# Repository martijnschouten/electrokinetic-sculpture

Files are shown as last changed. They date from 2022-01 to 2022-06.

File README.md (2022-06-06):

# Electrokinetic sculpture
This sculpture has been built as a demonstration of electrical friction compensation. The sculpture aims to create the same long-lasting mesmerizing effect as the work of [David C. Roy](https://www.woodthatworks.com/), but with cheap mechanical components, 3D printed parts and smart electronics. 

The sculpture currently has two modes. There is interactive mode in which it is possible to interact with the front wheel. In this cases the front wheel reacts as if it was connected to a passive system with little friction and a large moment of inertia. To see a video of the interactive mode click [here](https://youtu.be/oQwkW7BH-mE). The second mode is a zen mode in this mode the sculpture just rotates slowly, a video of this mode can be found [here](https://youtu.be/FcRmKU-JQ9s "Video on Youtube")

PXL_20220102_092019050-2 MP (https://youtu.be/oQwkW7BH-mE "Video on Youtube")

For a more detailed description of the project see the [hackaday page](https://hackaday.io/project/183344-electrokinetic-sculpture).

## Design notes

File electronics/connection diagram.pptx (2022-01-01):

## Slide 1

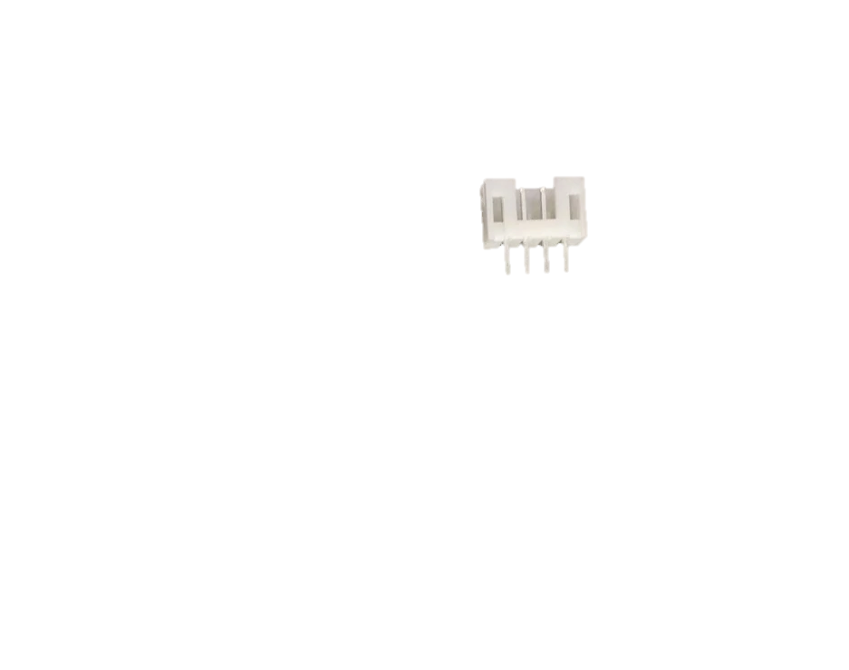
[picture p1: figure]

Charging port

Front wheel

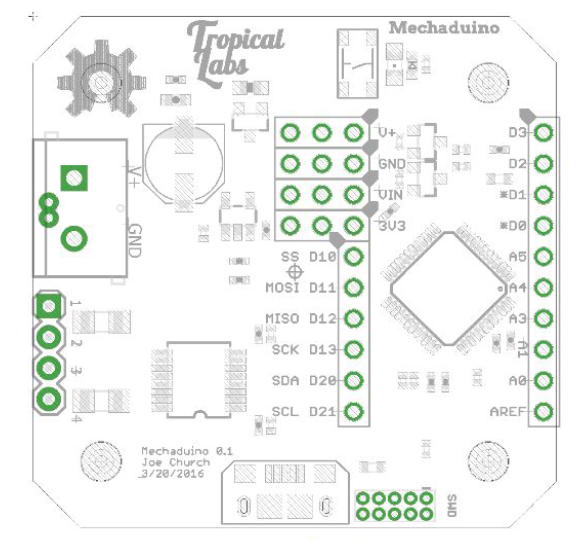
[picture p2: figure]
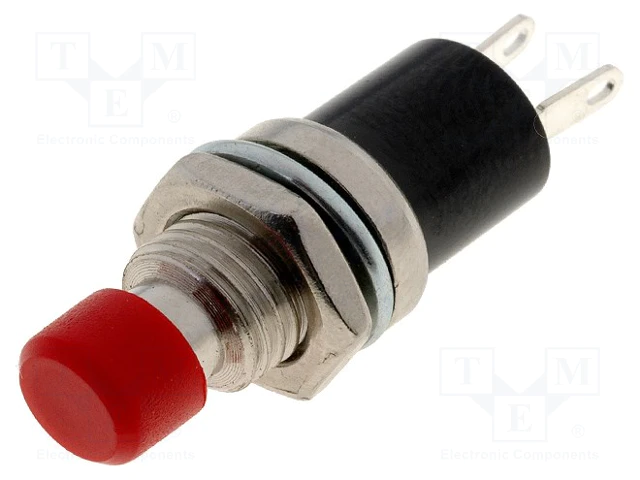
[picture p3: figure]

Program button

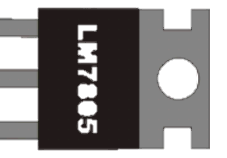
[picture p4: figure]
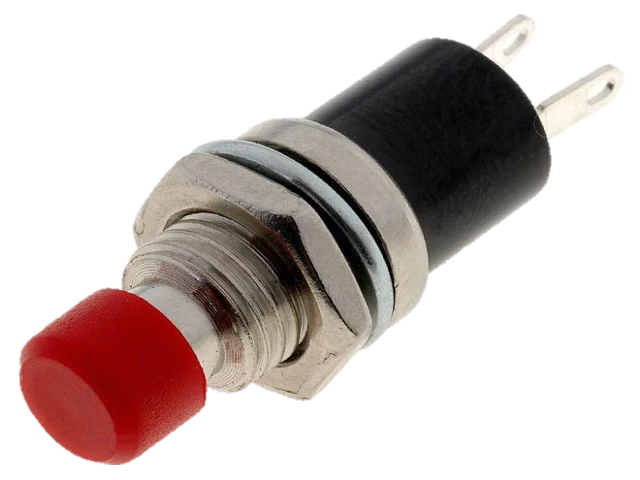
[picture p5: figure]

Mode Select

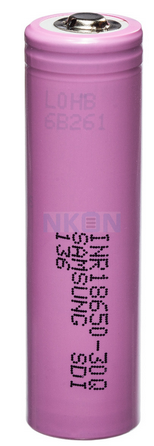
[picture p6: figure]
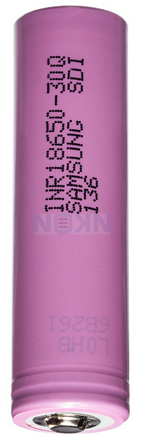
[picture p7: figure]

BMS

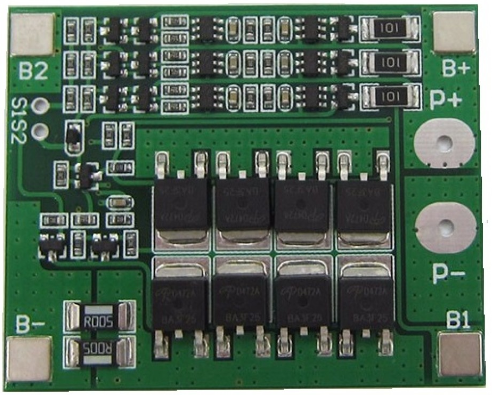
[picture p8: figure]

On/Off
Switch

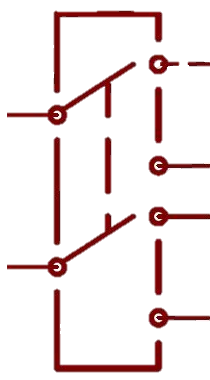
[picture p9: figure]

Back wheel

Program button

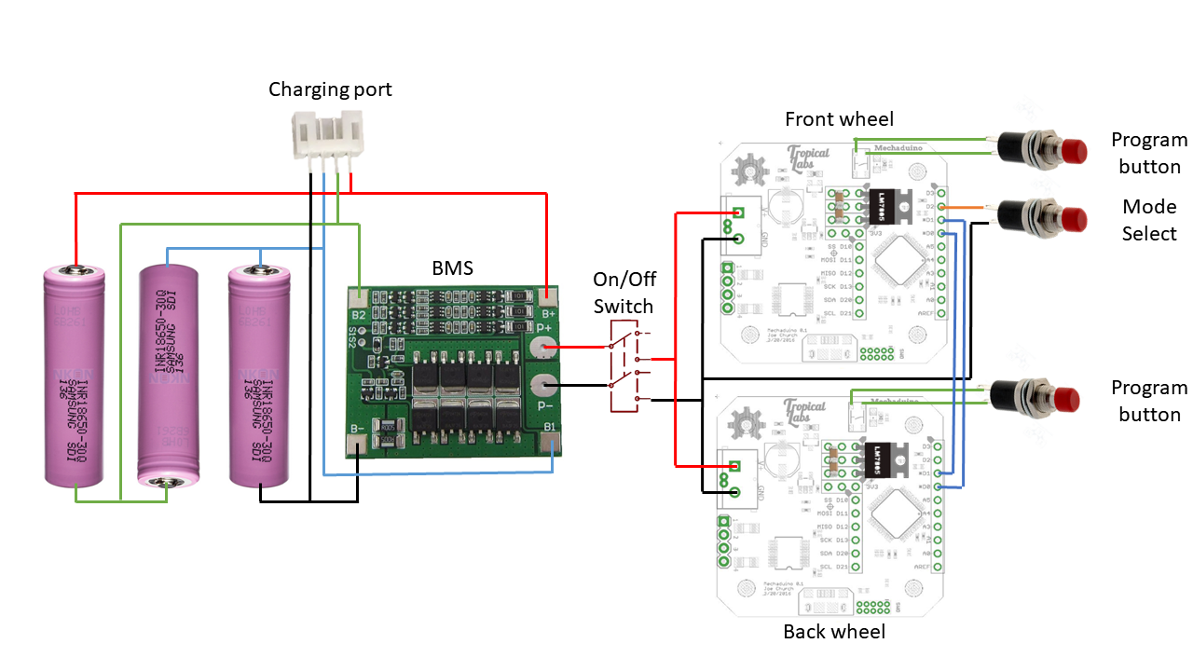
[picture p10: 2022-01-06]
electronics/connection diagram.png

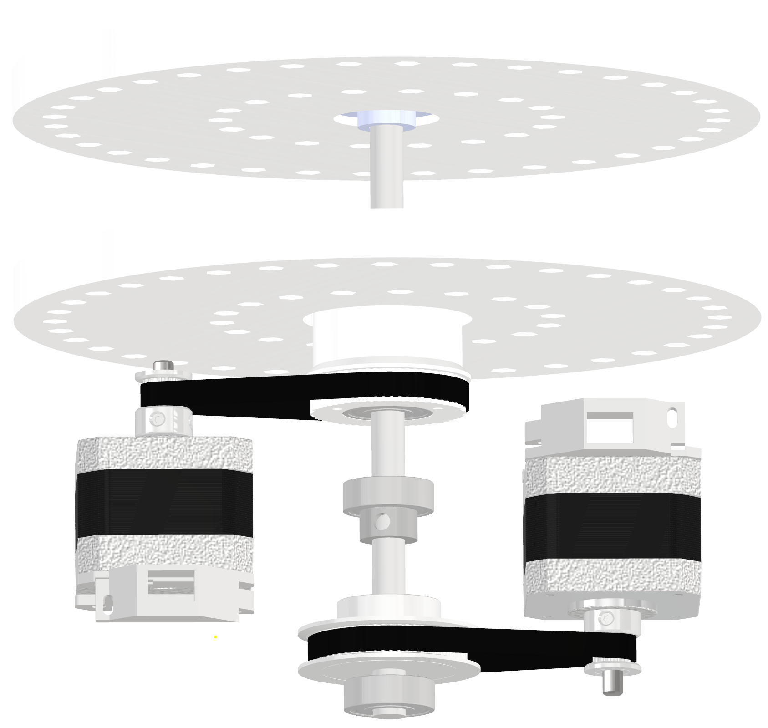
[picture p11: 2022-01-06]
cad files/mechanics view.png

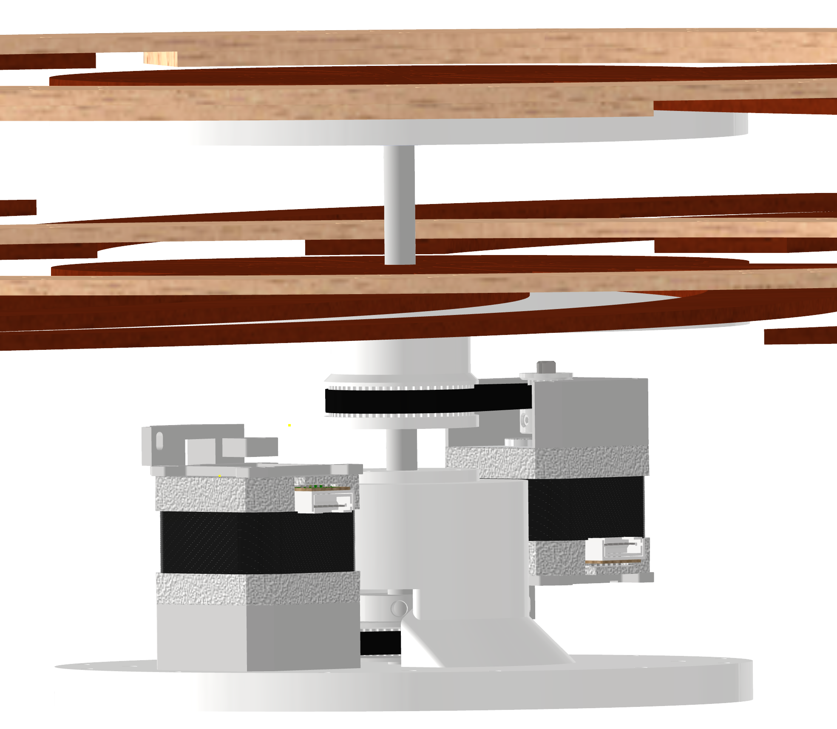
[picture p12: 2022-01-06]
cad files/inside view.png

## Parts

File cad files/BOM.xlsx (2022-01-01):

123-3d
1 | BMS | 4.5 | 2.95 | 7.45 | https://www.tinytronics.nl/shop/en/batteries/other/li-ionli-po-protection-circuit-(bms)-3s
2 | Stepper | 12.5 | 6.95 | 31.95 | https://www.123-3d.nl/123-3D-NEMA17-stappenmotor-1-8-graden-per-stap-40-mm-lang-4-08-kg-cm-SL42S240A105-0524-i3421-t14804.html
1 | pulley 60 teeth | 10 | 0 | 10 | https://www.123-3d.nl/123-3D-GT2-Pulley-hoge-resolutie-6-mm-riem-60-tanden-8-mm-as-i2572-t14819.html
2 | pulley 16 teeth | 6 | 0 | 12 | https://www.123-3d.nl/123-3D-GT2-Pulley-hoge-resolutie-6-mm-riem-16-tanden-5-mm-as-14-mm-hoog-6GT2DR16T5MMD-i2114-t14815.html
1 | mounting hub | 8 | 2.95 | 10.95 | https://opencircuit.shop/Product/Pololu-Universal-Aluminum-Mounting-Hub-8mm
3 |  | 2.75 | 0 | 8.25 | https://www.123-3d.nl/123-3D-Metaalschroef-inbus-M3x20-cilinderkop-verzinkt-50-stuks-i1175-t3122.html
2 |  | 2.25 | 0 | 4.5 | https://www.123-3d.nl/123-3D-Metaalschroef-inbus-M3x12-cilinderkop-verzinkt-50-stuks-i1173-t3122.html
2 |  | 2.5 | 0 | 5 | https://www.123-3d.nl/123-3D-Zeskantmoer-verzinkt-M3-100-stuks-i130-t3042.html
4 |  | 0.75 | 0 | 3 | https://www.123-3d.nl/123-3D-Kogellager-608ZZ-DME00003-i20-t13131.html
1 |  | 27.5 | 0 | 27.5 | https://www.123-3d.nl/123-3D-Filament-wit-1-75-mm-PETG-1-kg-Jupiter-serie-DFE02013c-i1907-t7395.html
1 |  | 12.5 | 0 | 12.5 | https://www.123-3d.nl/123-3D-Lineaire-as-staaf-gehard-en-geslepen-met-chroomlaag-8x250-mm-i1775-t13814.html
2 |  | 5.95 | 2.95 | 14.85 | https://www.kiwi-electronics.nl/panel-mount-usb-b-naar-micro-b-kabel?lang=en
 |  |  |  | 100 | laser cutting
 |  |  |  | 247.95
additional
1 |  | 13.99 | 6.95 | 20.94 | https://www.conrad.nl/p/voltcraft-eco-lipo-1000-modelbouw-oplader-230-v-1-a-li-poly-1460626
china
1 | BMS | 4.5 | 2.95 | 7.45 | https://www.tinytronics.nl/shop/en/batteries/other/li-ionli-po-protection-circuit-(bms)-3s
2 | Stepper | 12.5 | 6.95 | 31.95 | https://www.123-3d.nl/123-3D-NEMA17-stappenmotor-1-8-graden-per-stap-40-mm-lang-4-08-kg-cm-SL42S240A105-0524-i3421-t14804.html
1 | pulley 60 teeth | 1 | 2.22 | 3.22 | https://www.123-3d.nl/123-3D-GT2-Pulley-hoge-resolutie-6-mm-riem-60-tanden-8-mm-as-i2572-t14819.html
2 | pulley 16 teeth | 0.7 | 2.22 | 3.62 | https://www.aliexpress.com/item/32950478691.html
1 | mounting hub | 8 | 2.95 | 10.95 | https://opencircuit.shop/Product/Pololu-Universal-Aluminum-Mounting-Hub-8mm
3 |  | 2.75 | 0 | 8.25 | https://www.123-3d.nl/123-3D-Metaalschroef-inbus-M3x20-cilinderkop-verzinkt-50-stuks-i1175-t3122.html
2 |  | 2.25 |  | 4.5 | https://www.123-3d.nl/123-3D-Metaalschroef-inbus-M3x12-cilinderkop-verzinkt-50-stuks-i1173-t3122.html
2 |  | 2.5 |  | 5 | https://www.123-3d.nl/123-3D-Zeskantmoer-verzinkt-M3-100-stuks-i130-t3042.html
4 |  | 0.75 |  | 3 | https://www.123-3d.nl/123-3D-Kogellager-608ZZ-DME00003-i20-t13131.html
1 |  | 27.5 |  | 27.5 | https://www.123-3d.nl/123-3D-Filament-wit-1-75-mm-PETG-1-kg-Jupiter-serie-DFE02013c-i1907-t7395.html
1 |  | 4 |  | 4 | https://www.123-3d.nl/123-3D-Lineaire-as-staaf-gehard-en-geslepen-met-chroomlaag-8x250-mm-i1775-t13814.html
2 |  | 5.95 | 2.95 | 14.85 | https://www.kiwi-electronics.nl/panel-mount-usb-b-naar-micro-b-kabel?lang=en
 |  |  |  | 100 | laser cutting
 |  |  |  | 224.29

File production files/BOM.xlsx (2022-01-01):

Needed | Name | Units | Cost | Shipping | Total | Link
1 | Li-ion/Li-Po Protection circuit (BMS) - 3S - with Balancing | 1 | 4.5 | 2.95 | 7.45 | https://www.tinytronics.nl/shop/en/batteries/other/li-ionli-po-protection-circuit-(bms)-3s
2 | NEMA17, 40mm long 1,8 degree per step | 2 | 12.5 | 6.95 | 31.95 | https://www.123-3d.nl/123-3D-NEMA17-stappenmotor-1-8-graden-per-stap-40-mm-lang-4-08-kg-cm-SL42S240A105-0524-i3421-t14804.html
1 | GT2 Pulley, 6 mm belt, 60 teeth, 8 mm axis | 1 | 10 | 0 | 10 | https://www.123-3d.nl/123-3D-GT2-Pulley-hoge-resolutie-6-mm-riem-60-tanden-8-mm-as-i2572-t14819.html
2 | GT2 Pulley, 6 mm belt, 16 teeth, 5 mm axis, 14 mm long | 2 | 6 | 0 | 12 | https://www.123-3d.nl/123-3D-GT2-Pulley-hoge-resolutie-6-mm-riem-16-tanden-5-mm-as-14-mm-hoog-6GT2DR16T5MMD-i2114-t14815.html
1 | Pololu Universal Aluminum Mounting Hub for 8mm Shaft, M3 Holes | 1 | 8 | 2.95 | 10.95 | https://opencircuit.shop/Product/Pololu-Universal-Aluminum-Mounting-Hub-8mm
186 | m3 x 16 50pcs | 4 | 2.7 | 0 | 10.8 | https://www.123-3d.nl/123-3D-Metaalschroef-inbus-M3x16-cilinderkop-verzinkt-50-stuks-i1174-t3122.html
168 | m3 locknut 100pcs | 2 | 3.2 | 0 | 6.4 | https://www.123-3d.nl/123-3D-Borgmoer-verzinkt-M3-100-stuks-i132-t3043.html
8 | m3 x 35 50 pcs | 1 | 3.5 | 0 | 3.5 | https://www.123-3d.nl/123-3D-Metaalschroef-inbus-M3x35-cilinderkop-verzinkt-50-stuks-i1178-t3122.html
4 | 608ZZ ball bearing | 4 | 0.75 | 0 | 3 | https://www.123-3d.nl/123-3D-Kogellager-608ZZ-DME00003-i20-t13131.html
2 | 1kg PLA white | 2 | 27.5 | 0 | 55 | https://www.123-3d.nl/123-3D-Filament-wit-1-75-mm-PETG-1-kg-Jupiter-serie-DFE02013c-i1907-t7395.html
1 | 8x250 mm axis | 1 | 12.5 | 0 | 12.5 | https://www.123-3d.nl/123-3D-Lineaire-as-staaf-gehard-en-geslepen-met-chroomlaag-8x250-mm-i1775-t13814.html
2 | Panel Mount USB B to Micro-B cable | 2 | 5.95 | 2.95 | 14.85 | https://www.kiwi-electronics.nl/en/panel-mount-usb-b-to-micro-b-cable-901
1 | laser cutting, 6mm Birch Plywood | 1 | 181 | 0 | 181 | https://snijlab.nl/
2 | GT2 timing belt, 6 mm, closed, 188 mm | 2 | 3.5 | 0 | 7 | https://www.123-3d.nl/123-3D-GT2-timing-belt-6-mm-gesloten-188-mm-i2748-t3046.html
1 | VOLTCRAFT Eco LiPo 1000 charger | 1 | 13.99 | 6.95 | 20.94 | https://www.conrad.nl/p/voltcraft-eco-lipo-1000-modelbouw-oplader-230-v-1-a-li-poly-1460626
2 | Mechaduino | 2 | 49 | 0 | 98 | https://tropical-labs.com/shop/mechaduino-0-2-pcb/
3 | PS-01 red push button | 1 | 1.19 | 0 | 1.19 | https://www.tme.eu/en/details/ps-01/standard-switches/
1 | TSX103 dpdt switch 3A | 1 | 1.17 | 0 | 1.17 | https://www.tme.eu/en/details/tsx103/toggle-switches/ninigi/
2 | JST PH 4P | 1 | 1.27 | 1.99 | 3.26 | https://www.aliexpress.com/item/4000091077742.html
3 | Samsung INR18650-30Q 3000mAh - 15A button top | 3 | 7.95 | 0 | 23.85 | https://www.nkon.nl/samsung-inr-18650-30q-3000mah-button-top.html
3 | 10pcs 18650 Battery holder | 1 | 5.51 | 0 | 5.51 | https://www.aliexpress.com/item/32858162000.html
400ml | Rambo warm oak silk | 1 | 28.99 | 0 | 28.99 | https://www.karwei.nl/assortiment/rambo-pantserlak-interieur-transparant-zijdeglans-warm-eiken-750-ml/p/B607934
150ml | cetabever transparent silk | 1 | 24.49 | 0 | 24.49 | https://www.karwei.nl/assortiment/cetabever-binnenbeits-transparant-zijdeglans-beuken-750-ml/p/B183112
2 | L7805abv voltage regulator | 2 | 0.33 | 0 | 0.66 | https://www.tme.eu/en/details/l7805abv/unregulated-voltage-regulators/stmicroelectronics/
4 | 0805 1uF capacitor | 4 | 0.01 | 0 | 0.04
 |  |  |  |  | 574.5

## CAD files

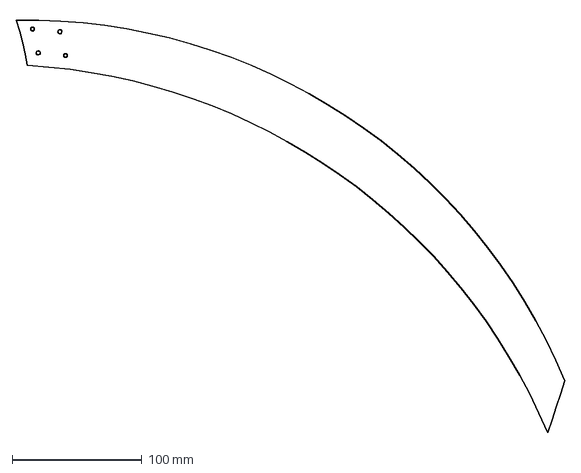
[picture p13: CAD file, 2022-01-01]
production files/laser cutting/6x spoke4 6mm.dxf
423.3 x 321.5 mm

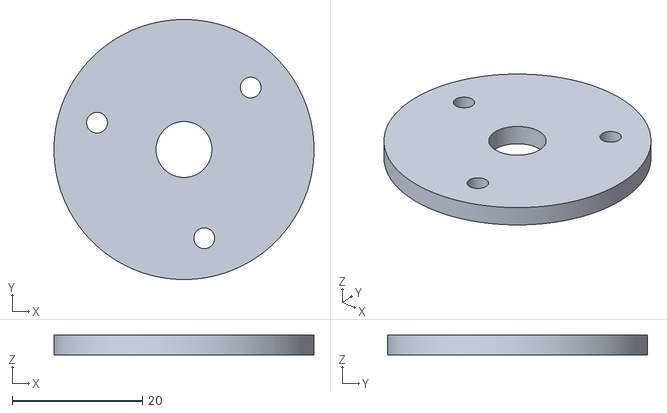
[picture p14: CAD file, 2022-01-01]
production files/stls/sculpture_bearing_holder.stl
40.0 x 40.0 x 3.00

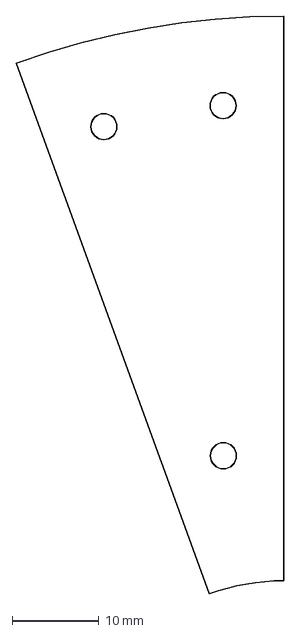
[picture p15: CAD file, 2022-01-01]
production files/laser cutting/12x cover 6mm.dxf
30.8 x 66.5 mm

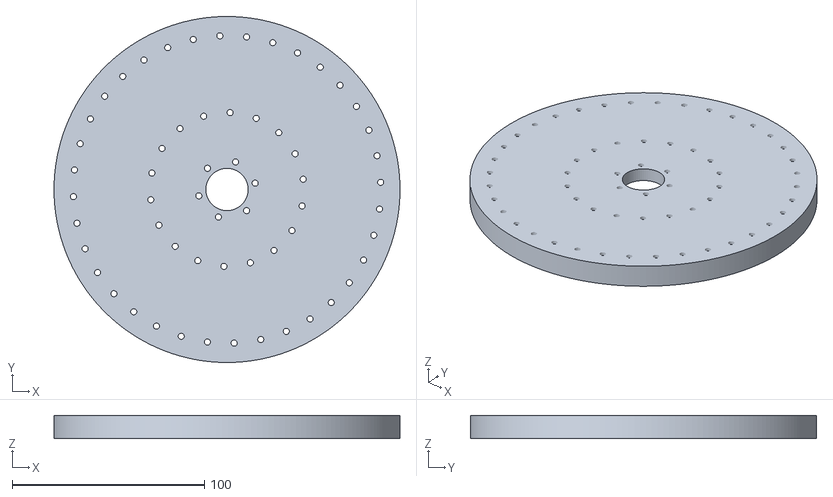
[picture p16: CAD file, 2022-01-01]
production files/stls/sculpture_pulley1.stl
180.0 x 180.0 x 12.0

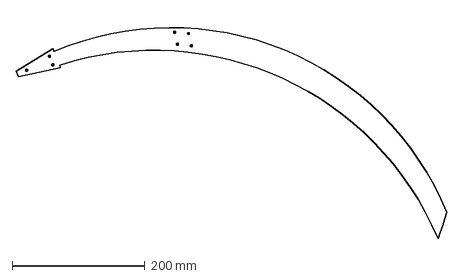
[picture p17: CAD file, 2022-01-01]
production files/laser cutting/6x spoke 6mm.dxf
649.7 x 335.7 mm

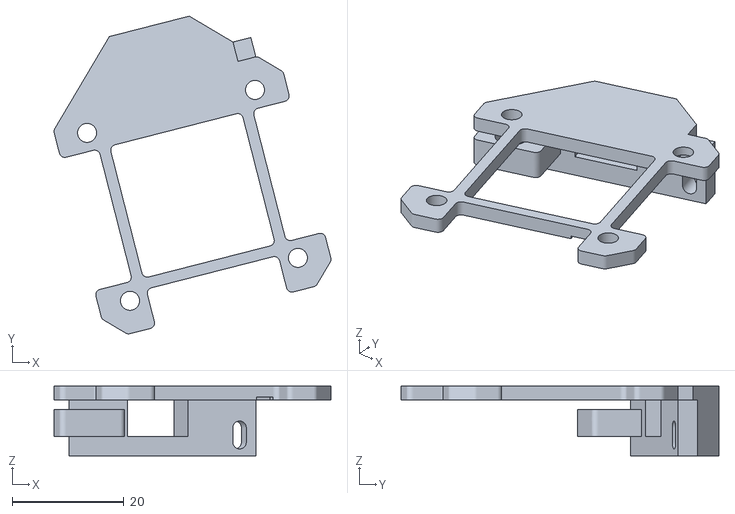
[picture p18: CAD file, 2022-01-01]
production files/stls/sculpture_mechaduino_mount3.stl
49.5 x 56.8 x 12.5

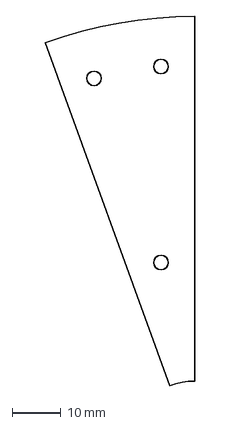
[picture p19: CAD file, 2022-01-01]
production files/laser cutting/12x cover2 6mm.dxf
30.8 x 75.9 mm

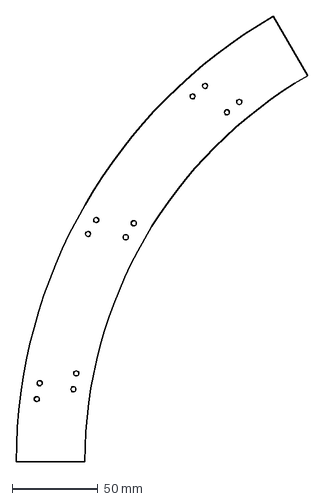
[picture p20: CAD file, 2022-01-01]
production files/laser cutting/4x wheel6 6mm.dxf
170.0 x 259.8 mm

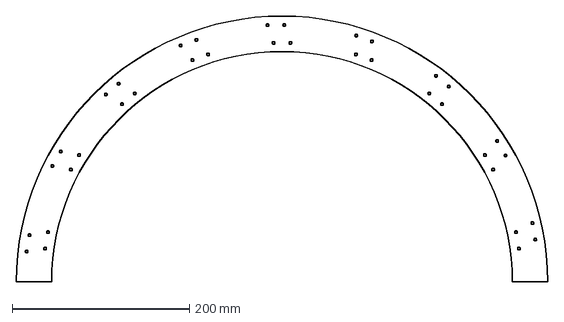
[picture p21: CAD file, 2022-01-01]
production files/laser cutting/4x wheel 6mm.dxf
600.0 x 300.0 mm

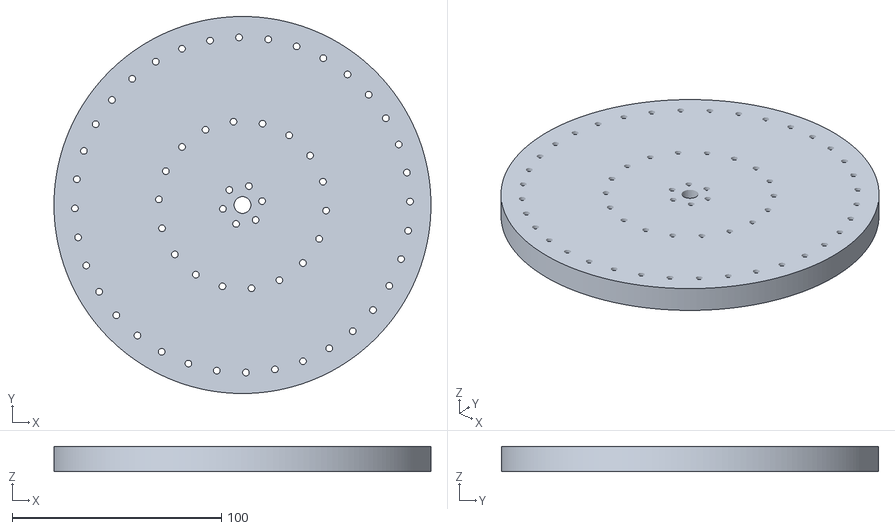
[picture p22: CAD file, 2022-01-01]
production files/stls/sculpture_front_plate.stl
180.0 x 180.0 x 12.0

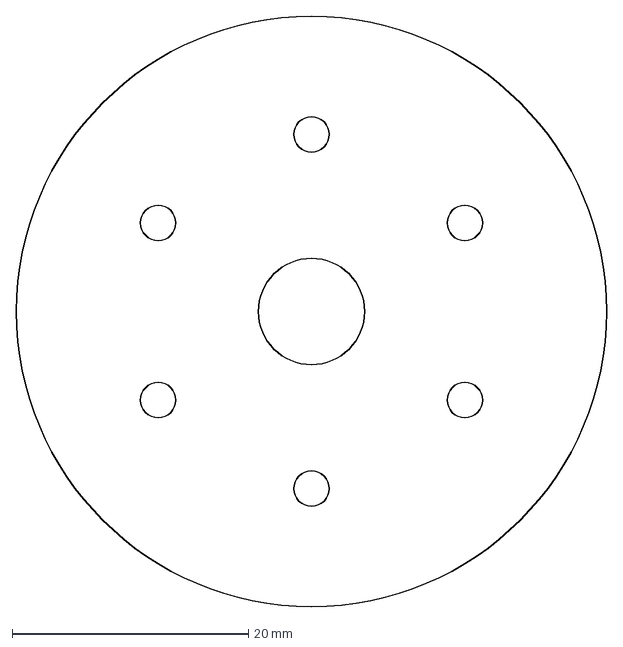
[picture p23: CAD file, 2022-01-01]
production files/laser cutting/1x circle2 6mm.dxf
50.0 x 50.0 mm

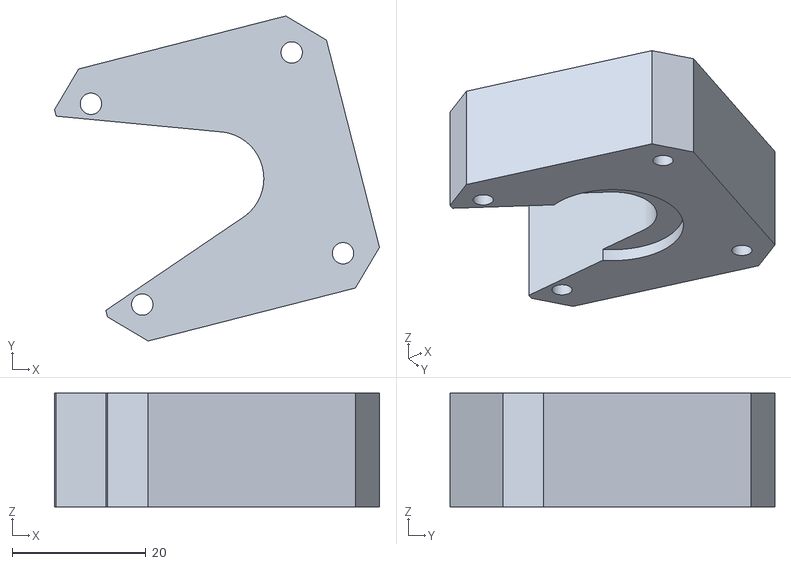
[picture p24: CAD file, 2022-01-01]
production files/stls/sculpture_motor_spacer_1.stl
48.6 x 48.6 x 17.0

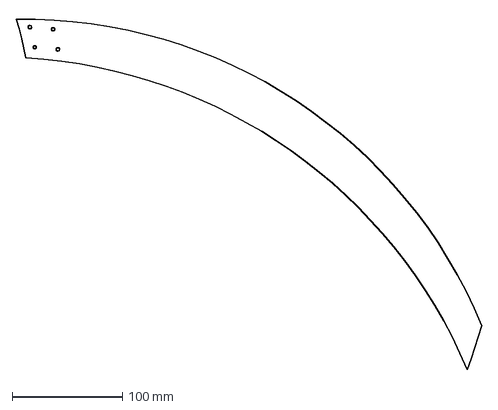
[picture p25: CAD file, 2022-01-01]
production files/laser cutting/6x spoke2 6mm.dxf
423.3 x 321.5 mm

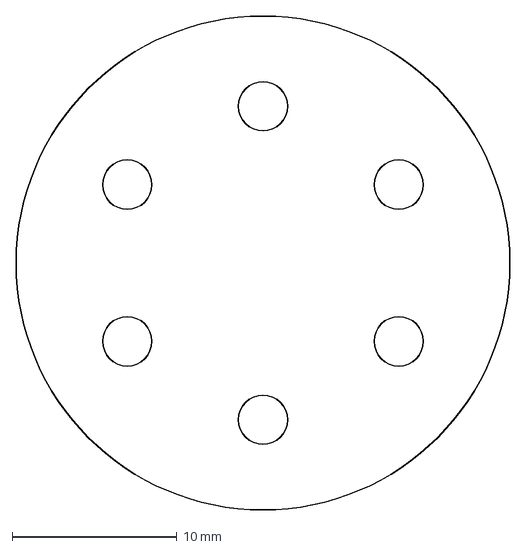
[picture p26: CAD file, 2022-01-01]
production files/laser cutting/1x circle 6mm.dxf
30.0 x 30.0 mm

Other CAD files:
production files/stls/sculpture_bearing_holder2.stl
production files/stls/sculpture_mechaduino_mount3_1.stl
production files/stls/sculpture_motor_spacer.stl
production files/stls/sculpture_wall_mount.stl
cad files/Assembly1.iam
cad files/GT2 60 teeth pulley.ipt
cad files/GT2_16T.ipt
cad files/Lock Collar 8mm.ipt
cad files/Nema 17 - Busheng 17HD34008-22B/ANSI B27.7 - 53.9(1).ipt
cad files/Nema 17 - Busheng 17HD34008-22B/BS 3469 - 02 - 5 x 16 x 5.ipt
cad files/Nema 17 - Busheng 17HD34008-22B/EN ISO 7045 - M3 x 25H.ipt
cad files/Nema 17 - Busheng 17HD34008-22B/Nema 17 Base Cap.ipt
cad files/Nema 17 - Busheng 17HD34008-22B/Nema 17 Central Spacer.ipt
cad files/Nema 17 - Busheng 17HD34008-22B/Nema 17 Coil.ipt
cad files/Nema 17 - Busheng 17HD34008-22B/Nema 17 PCB.ipt
cad files/Nema 17 - Busheng 17HD34008-22B/Nema 17 Plastic Spacer 1.ipt
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

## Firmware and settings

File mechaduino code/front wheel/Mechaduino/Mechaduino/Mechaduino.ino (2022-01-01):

 /*
  Author: Martijn Schouten
  Contact: https://github.com/martijnschouten/

  To use this program you first need to calibrate your mechaduino. To do so:
  - Upload the project in the for calibration folder
  - Go to the serial monitor and connect to your mechaduino
  - Start the calibration routine by sending c to your mechaduino. Make sure it is free to rotate.
  - Copy the outputted encoder lookup table to parameters.cpp

  To make this run stably on your hardware you may have to tune T_static, d_term (current file) and vKp, vKi, vKd (parameters.cpp)
*/

#include "Utils.h"
#include "Parameters.h"
#include "State.h"
#include "analogFastWrite.h"
#include <arduino-timer.h>


//////////////////////////////////////
/////////////////SETUP////////////////
//////////////////////////////////////

//Velocity calculation
float yw_old = 0;         //Last measured position
float v_loc = 0;          //Low pass filtered velocity estimate
float v_a = 0.7265;       //a coefficient of the low pass filter on the velocity
float v_b = 0.1367;       //b coefficient of the low pass filter on the velocity

//Acceleration calculation
float v_old = 0;          //Last calculated velocity
float a_loc = 0;          //Low pass filtered acceleration estimate
float a_a = 0.9691;       //a coefficient of the low pass filter on the acceleration
float a_b = 0.0155;       //b coefficient of the low pass filter on the acceleration

//Friction compensation
float T_static = 20;      //Estimate of the current needed to overcome the static friction in mA and divided by 8.6 
float v_idle = 0.04;      //Velocity above which the static friction compensation will become active
float p_term = 0.1;       //Determines the stiffness of the spring when rotated in the clockwise direction
float d_term = -10;       //Estimate of the dynamic friction
float m_term = 5000;      //Determines the additional moment of inertia

//Other variables
float set_point = 180;    //Will store the location where the wheel last turned in the counter-clockwise direction
int state = 0;            //state = 0 -> moving in the clockwise dirction, state = 1 -> moving in the counter-clockwise dirction
int timeout = 0;          //Before this variable reaches a certain treshhold, the output current will be kept zero in order to improve startup behaviour

//Variables used for switching between zen and interactive mode
int state2 = 0;           //state = 0 -> interactive mode. state = 1 -> zen mode
int latch_timer = 0;      //Timer for debouncing the button
int latch_timeout = 1000; //Timeout after which the button can be presed again (in ms)

Timer<1000, micros> timer;

bool control_loop(void *)
{
  //check if the mechaduino control loop isn't running
  if(mutex == true)
  {
      //if it is running quit this loop, to prevent lockup
      return true;
  }

  //calculate velocity, and low pass filter
  v_loc = v_a*v_loc + v_b*(yw-yw_old);
  a_loc = a_a*a_loc + a_b*(v_loc-v_old);

  if (state2 == 0 || state2 == 1)
  {
      //Check if the mode button has been pressed recently
      if (latch_timer < latch_timeout)
      {
        latch_timer++;
      }
      else
      {
        //if that's not the case, check if it is pressed and if so switch mode
        if (state2 == 0)
        {
          if (!digitalRead(2))
          {
             state2 = 1;
          }
        }
        else
        {
           if (digitalRead(2))
          {
             mode = 'v';
             state2 = 2;
             latch_timer = 0;
          }
        }
      }   
    
    //switch from moving with positive v to moving with negative v
    if ((state == 0) and(v_loc < -v_idle))
    {         
      state = 1;//switch to moving with negative v
    }
    //switch from moving with negative v to moving with positive v
    if ((state == 1) and (v_loc > v_idle))
    {         
      state = 0;//switch to moving with negative v
    }
  
    //apply non-linear equation
    if (yw < set_point)
    {
      r = -p_term*(yw-set_point)-d_term*v_loc-m_term*a_loc;
    }
    else
    {
       r = -d_term*v_loc-m_term*a_loc;
    }
    
    if ((state == 1) and (yw>set_point)){
        set_point = yw;//lock the setpoint
    }
  
  
    //static friction compensation
    if (state == 0)
    {
       r = r + T_static;
    }
    else 
    {
       r  = r - T_static;
    }

    //improve startup behaviour
    if (timeout<500)
    {
        r = 0;
        v_loc = 0;
        timeout++;
    }
  }
  else
  {
      //Check if the mode button has been pressed recently
      if (latch_timer < latch_timeout)
      {
        latch_timer++;
      }
      else
      {
        //if that's not the case, check if it is pressed and if so switch mode
        if (state2 == 2)
        {
          if (!digitalRead(2))
          {
             state2 = 3;
          }
        }
        else
        {
           if (digitalRead(2))
          {
             state2 = 0;
             latch_timer = 0;
             mode = 't';
          }
        }
      }

      //in zen mode, just move the both wheels slowly
      r = 2.5;
      v_loc = 0.025;
  }

  //Send the current torque out over usb for debug purposes
  SerialUSB.println(r);
  
  //Send the current velocity to the other mechaduino so it can mirror it
  Serial1.println(v_loc);

  //Store current values, for use in the low pass filters
  yw_old = yw;
  v_old = v_loc;
  return true;
}

void setup()        // This code runs once at startup
{
  u = 0;                        
  digitalWrite(ledPin,HIGH);        // turn LED on 
  setupPins();                      // configure pins
  setupTCInterrupts();              // configure controller interrupt

  SerialUSB.begin(115200);          // start debug serial connection
  Serial1.begin(115200);            // start serial connection with the other mechaduino
  delay(3000);                      // This delay seems to make it easier to establish a connection when the Mechaduino is configured to start in closed loop mode.  
  setupSPI();                       // Sets up SPI for communicating with encoder
  
  digitalWrite(ledPin,LOW);         // turn LED off 
  pinMode(2, INPUT_PULLUP);         // enable the pullup on the mode button

  
  // spot check some of the lookup table to decide if it has been filled in
  if (lookup[0] == 0 && lookup[128] == 0 && lookup[1024] == 0)
    SerialUSB.println("WARNING: Lookup table is empty! Run calibration");

  enableTCInterrupts();             // start in closed loop 
  mode = 't';                       // start in torque mode
  r = 0;                            // start with no torque
  
  timer.every(1, control_loop);     //run the control loop every time timer.tick() is called
}
  


//////////////////////////////////////
/////////////////LOOP/////////////////
//////////////////////////////////////


void loop()                 // main loop
{
  delayMicroseconds(1000);//necessary to give the control loops of the mechaduino time to run
  timer.tick();//run the control loop
}

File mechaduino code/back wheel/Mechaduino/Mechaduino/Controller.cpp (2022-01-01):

//Contains TC5 Controller definition
//The main control loop is executed by the TC5 timer interrupt:

#include <SPI.h>

#include "State.h"
#include "Utils.h"
#include "Parameters.h"


void TC5_Handler() {                // gets called with FPID frequency
  
  static int print_counter = 0;               //this is used by step response

  if (TC5->COUNT16.INTFLAG.bit.OVF == 1) {    // A counter overflow caused the interrupt
     
    TEST1_HIGH();  //digitalWrite(3, HIGH);       //Fast Write to Digital 3 for debugging

    y = lookup[readEncoder()];                    //read encoder and lookup corrected angle in calibration lookup table
   
    if ((y - y_1) < -180.0) wrap_count += 1;      //Check if we've rotated more than a full revolution (have we "wrapped" around from 359 degrees to 0 or ffrom 0 to 359?)
    else if ((y - y_1) > 180.0) wrap_count -= 1;

    yw = (y + (360.0 * wrap_count));              //yw is the wrapped angle (can exceed one revolution)


    if (mode == 'h') {                            //choose control algorithm based on mode
      hybridControl();                            // hybrid control is still under development...
    }
    else {
      switch (mode) {
        case 'x':         // position control                        
            e = (r - yw);
            
            ITerm += (pKi * e);                             //Integral wind up limit
            if (ITerm > 150.0) ITerm = 150.0;
            else if (ITerm < -150.0) ITerm = -150.0;          
           
            DTerm = pLPFa*DTerm -  pLPFb*pKd*(yw-yw_1);
           
            u = (pKp * e) + ITerm + DTerm;
           
           
            break;
            
        case 'v':         // velocity controlr
          v = vLPFa*v +  vLPFb*(yw-yw_1);     //filtered velocity called "DTerm" because it is similar to derivative action in position loop

          e = (r - v);   //error in degrees per rpm (sample frequency in Hz * (60 seconds/min) / (360 degrees/rev) )

          ITerm += (vKi * e);                 //Integral wind up limit
          if (ITerm > 200) ITerm = 200;
          else if (ITerm < -200) ITerm = -200;
        
          u = ((vKp * e) + ITerm - (vKd * (e-e_1)));
          
          //SerialUSB.println(e);
          break;
          
        case 't':         // torque control
          u = 1.0 * r ;
          break;
        default:
          u = 0;
          break;
      }

    y_1 = y;  //copy current value of y to previous value (y_1) for next control cycle before PA angle added

    
    if (u > 0)          //Depending on direction we want to apply torque, add or subtract a phase angle of PA for max effective torque.  PA should be equal to one full step angle: if the excitation angle is the same as the current position, we would not move!  
      {                 //You can experiment with "Phase Advance" by increasing PA when operating at high speeds
      y += PA;          //update phase excitation angle
      if (u > uMAX)     // limit control effort
        u = uMAX;       //saturation limits max current command
      }
    else
      {
      y -= PA;          //update phase excitation angle
      if (u < -uMAX)    // limit control effort
        u = -uMAX;      //saturation limits max current command
      }

      U = abs(u);       //

      if (abs(e) < 0.1) ledPin_HIGH();    // turn on LED if error is less than 0.1
      else ledPin_LOW();                  //digitalWrite(ledPin, LOW);


      output(-y, round(U));    // update phase currents
    }
    
   // e_3 = e_2;    //copy current values to previous values for next control cycle
    e_2 = e_1;    //these past values can be useful for more complex controllers/filters.  Uncomment as necessary    
    e_1 = e;
   // u_3 = u_2;
    u_2 = u_1;
    u_1 = u;
    yw_1 = yw;
    //y_1 = y;
    
    if (print_yw ==  true){       //for step resonse... still under development
      print_counter += 1;  
      if (print_counter >= 5){    // print position every 5th loop (every time is too much data for plotter and may slow down control loop
        SerialUSB.println(int(yw*1024));    //*1024 allows us to print ints instead of floats... may be faster
        print_counter = 0;
      }
    }
    TC5->COUNT16.INTFLAG.bit.OVF = 1;    // writing a one clears the flag ovf flag
    TEST1_LOW();            //for testing the control loop timing

  }


}

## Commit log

2022-01-06 added belts and pulleys to the assembly
    [Assembly1.0045.iam, Assembly1.0051.iam, Assembly1.iam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]
2022-01-06 added step files
    [Assembly1.0051.iam, Assembly1.0052.iam, Assembly1.iam]
